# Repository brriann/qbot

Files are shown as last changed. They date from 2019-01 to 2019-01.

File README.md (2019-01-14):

# qbot
Build a Self-Driving Q-Bot using a Raspberry Pi Zero-W

Here is an overview of the project: https://medium.com/@michael_87060/build-a-self-driving-q-bot-6aa67ba60769

(and here is an older repo that supports a BeagleBone Blue: https://github.com/jvon-challenges/qbot)

The Q-bot is a small robot and associated software that uses machine learning (specifically Q learning) to learn how to complete a simple task (eg, seek the nearest object in its surroundings). The training can take place in a virtual or physical environment.

The build should cost <$50 with readily-available parts, and less if you salvage. The physical robot uses a Raspberry Pi Zero W, a Sparkfun VL53L1X laser time-of-flight sensor, and 28byj geared stepper motors for movement.  Aside from assorted nuts and bolts, a battery, and some wires, the only other required components can be 3D printed.  Links are provided below to the components you will need.  These are example products or vendors only; feel free to substitute parts wherever you like.  We are not endorsing, sponsored by,  or recommending any particular seller.

- Raspberry Pi Zero W: 
https://www.adafruit.com/product/3708

- 28byj Steppers with drivers: 
https://www.amazon.com/dp/B06X982PSL

- VL53L1x ToF distance sensor:
https://www.sparkfun.com/products/14722

- M3 hardware assortment:
https://www.amazon.com/gp/product/B07CZBR66J

- F to F dupont wires:
https://www.amazon.com/dp/B07GD2BWPY

For power, any small USB battery pack will be enought to run the bot. I used a 2S lipo 
battery and a BEC (battery eliminator) because I had them on hand for other projects, but
a small flat USB power bank is probably easier because no special charger is needed.

- USB battery pack:
https://www.amazon.com/dp/B076HJTNYJ/

- 2S lipo example:
https://www.amazon.com/dp/B07BJZZYBY

- BEC example: 
https://www.amazon.com/gp/product/B074PM59YS/

A video walkthrough of the build can be found here: https://youtu.be/-1W7-Q0RIaM

There are three example files included in this repo:

- example_virtual.py will create an instance of a virtual Q-bot and it will train to seek a randomly-generated virtual obstacle.  This example does not require a physical q-bot; you can run this on your laptop or desktop and it will render the virtual bot and its obstacle on screen using the python 'turtle'.

- example-physical.py will attempt to train the physical q-bot by looking around for an obstacle and learn to move closer to it by trial and error, improving as it goes

- example_virtual_physical will create a virtual q-bot, train it in software, and then use the learned Q-table values from the software training to have the physical Q-bot seek its nearest obstacle 

Enjoy the project files, and please reach out to us with questions, comments, and stories about your work with this project!  We can't wait to hear from you.

For hardware: jeff@loislab.org
For software: michael@loislab.org

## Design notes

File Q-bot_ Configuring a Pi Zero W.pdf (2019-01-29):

## Q-Bot: Configuring a Raspberry Pi Zero W

To run headless, optionally with Cloud9

This guide assumes you have a Raspberry Pi Zero W and want to set it up to run it headless (without a monitor and keyboard) on your wireless network. In my particular case, I’m using the Pi as the “brain” for the Q-bot robot; I want to connect to it using SSH wirelessly to control it, and I want to connect to a programming environment running on the Pi with a web browser.

Getting the Pi Zero operating on your network

1. Download the latest image of Raspbian Stretch Lite: https://www.raspberrypi.org/downloads/raspbian/
2. Using Etcher (or a similar image writing application), burn the image to your SD card
3. Mount the resulting burned SD image; you should see a boot volume with a number of files inside.
4. Create a new file called wpa_supplicant.conf in the root / directory of the boot partition (the smaller of the two partitions), with the following contents:

ctrl_interface=DIR=/var/run/wpa_supplicant GROUP=netdev
update_config=1
country=US

network={
ssid="YOURSSID"
psk="YOURPASSWORD"
scan_ssid=1
key_mgmt=WPA-PSK
}
5. Create an empty file called “ssh” in the root / directory of the boot partition of the SD card. The empty file will enable ssh, and will be deleted upon the next startup. Here are the notes from: https://www.raspberrypi.org/documentation/remote-access/ssh/

Enable SSH on a headless Raspberry Pi (add file to SD card on another machine)

For headless setup, SSH can be enabled by placing a file named ssh, without any extension, onto the boot partition of the SD card from another computer. When the Pi boots, it looks for the ssh file. If it is found, SSH is enabled and the file is deleted. The content of the file does not matter; it could contain text, or nothing at all.

If you have loaded Raspbian onto a blank SD card, you will have two partitions. The first one, which is the smaller one, is the boot partition. Place the file into this one.

6. Also in the root / directory of the boot partition, edit the config.txt file, and add the following lines at the end:
# Enable UART

enable_uart=1
7. Unmount the image and put the SD in the raspberry pi. Power it up and wait a couple of minutes.
8. If all goes well, the device will register it on your local network using mDNS and appear as “raspberrypi.local”. You can ping and ssh into the device now.
9. Alternatively: log into the Raspberry Pi using SSH:
user = pi, password = raspberry, ip address = [address on local subnet], example:
> pi@192.168.0.107
pi@192.168.0.107's password: raspberry

If the device doesn’t show up, then you need to go into troubleshooting mode. For example, if you’re working on a small local network where you don’t have a network admin to yell at you for running scans, you can power off the device and run an nmap scan (“sudo nmap -sn 192.168.0.0/24”) to identify devices on your local subnet. Boot the Pi Zero and scan again, and chances are that any new device is your Pi.

If THAT doesn’t work, try the following:
1. Try rebooting the Pi and see if that fixes it. Be patient on the first boot, it might take a few minutes.
2. Your wireless network might use a different authentication type. In the wpa_supplicant.conf file above, I was connecting to a network that used WPA Personal authentication, so I used the line “key_mgmt=WPA-PSK”. If you’re using WPA Enterprise, it needs to change to “key_mgmt=WPA-EAP”. If you’re using something else, google it.

Updating the OS and installing Cloud9
Cloud9 is a web-based development environment. It’s much more convenient when writing code for a project like the Q-bot compared to using something like a native editor like nano or vi in an SSH session. Setting it up takes some time, and consumes resources on a computer that isn’t exactly a powerhouse to begin with, so if you don’t want it or need it, feel free to skip ahead.
1. Reboot the Pi

2. Log into the Pi and run:

sudo apt-get update && sudo apt-get upgrade

Be patient, it might take a while.

3. From your home directory, grab the NodeJS ARM package and extract it to /usr/local:

cd ~

wget http://nodejs.org/dist/v0.10.28/node-v0.10.28-linux-arm-pi.tar.gz

tar -xzf ~/node-v0.10.28-linux-arm-pi.tar.gz

cd node-v0.10.28-linux-arm-pi/

sudo cp -rf * /usr/local

export NODE_PATH=”/usr/local/lib/node_modules”

4. Grab a copy of Cloud9 from Git and build it:

git clone git://github.com/c9/core.git c9sdk cd c9sdk
scripts/install-sdk.sh
5. Once that’s done, you can launch Cloud9 any time you want to use it by running the following command from the prompt:

~/c9sdk/server.js -l 0.0.0.0 -a : -w $MY_PROJECT_PATH &

Once all of those installations are complete, you should be able to use Cloud9 via web browser, and use the Adafruit library and example code to control servos and ESCs from the Pi.

Other Required Libraries

Update Python:

sudo apt-get update
sudo apt-get install -y python3 python3-pip python-dev sudo pip3 install rpi.gpio

Install support for i2c (a 2-wire serial protocol):

sudo apt-get install python-smbus sudo apt-get install i2c-tools

Python library for the vl53l1x laser distance sensor:

sudo pip3 install smbus2

sudo pip install vl53l1x

Install numpy:

sudo pip3 install numpy

Sometimes the install doesn’t work using pip3; if so, try:

sudo apt-get install python3-numpy

Enjoy the project files, and please reach out to us with questions, comments, and stories about your work with this project! We can't wait to hear from you.

For hardware: jeff@loislab.org
For software: michael@loislab.org

Reference:

This guide leans heavily on the information provided in the articles below. Thank you to the authors who shared their knowledge and made this guide (and the project overall) possible.

Adafruit’s guide Pi Zero W headless config: https://learn.adafruit.com/raspberry-pi-zero-creation/overview

Chintan Pathak’s guide to installing Cloud9 on a Raspberry Pi: https://medium.com/@chintanp/using-cloud9-3-0-ide-on-raspberry-pi-954cf2d6ab8e

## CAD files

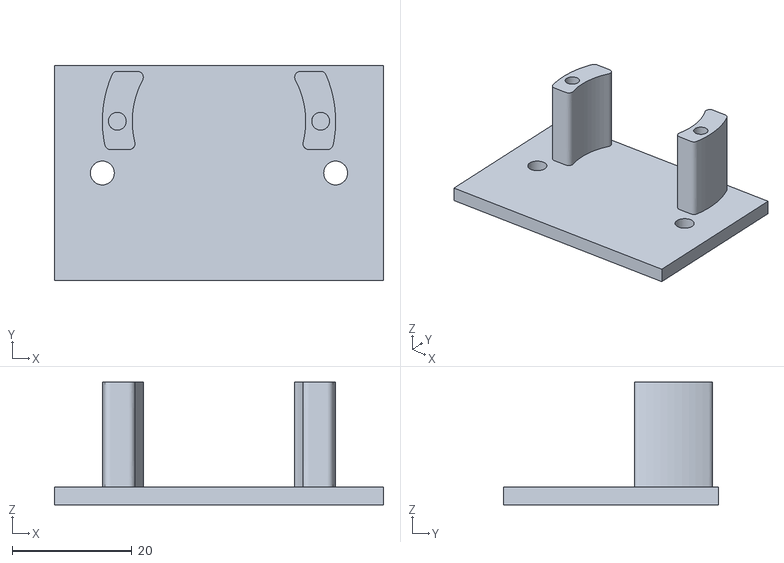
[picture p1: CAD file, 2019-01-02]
CAD/28byj sensor mount.stl
55.0 x 36.0 x 20.5

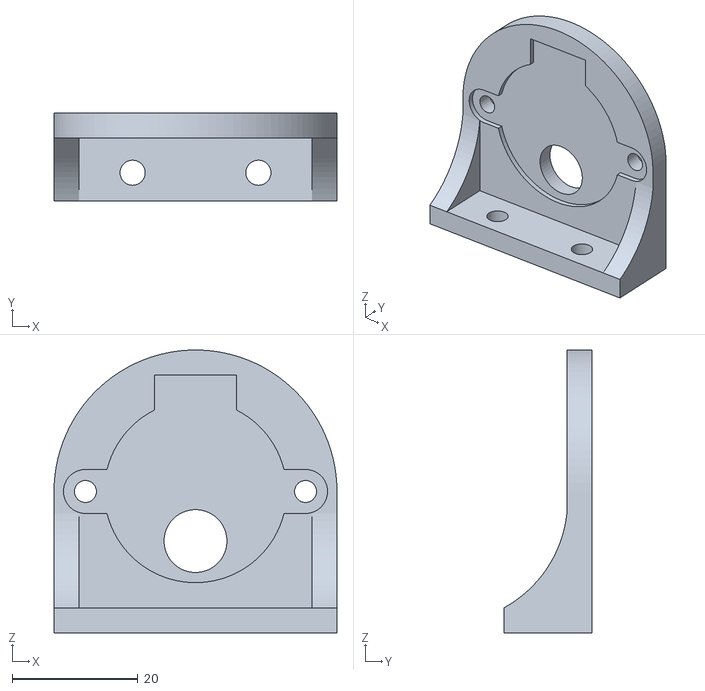
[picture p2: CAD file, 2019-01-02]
CAD/28byj bracket.stl
45.0 x 14.0 x 45.0

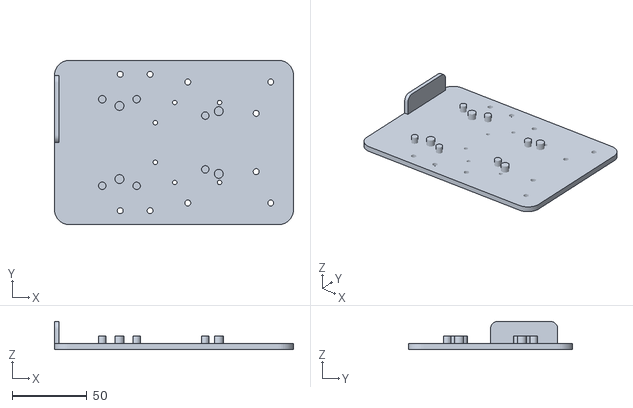
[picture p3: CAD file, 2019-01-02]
CAD/Qbot frame Rev3.stl
160.0 x 110.0 x 19.0

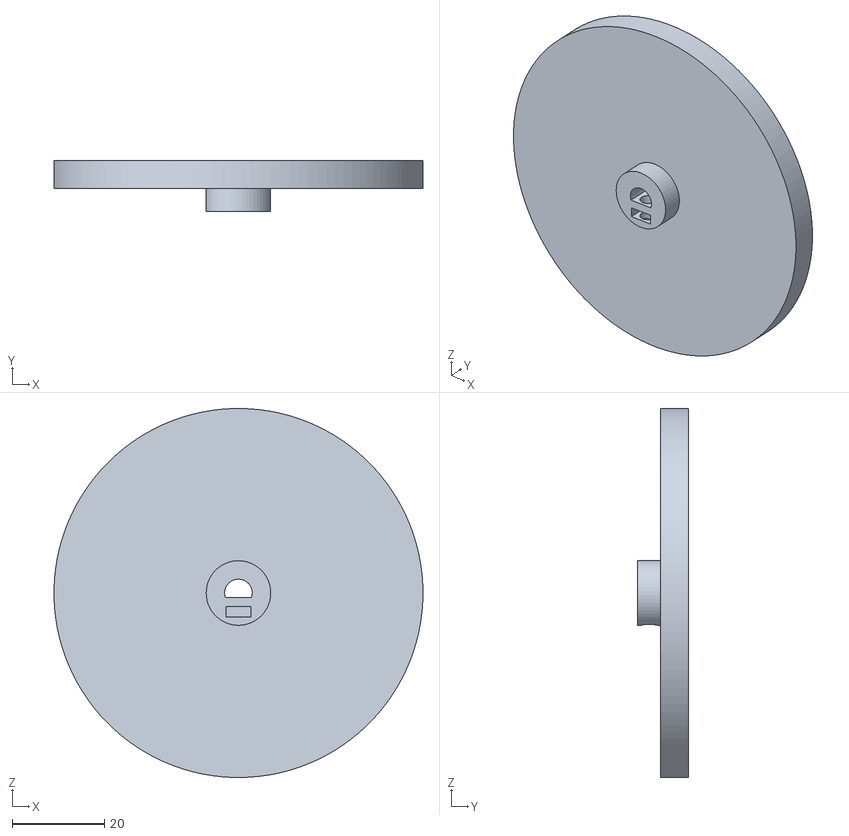
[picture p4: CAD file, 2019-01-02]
CAD/Qbot wheel Rev2.stl
80.0 x 11.0 x 80.0

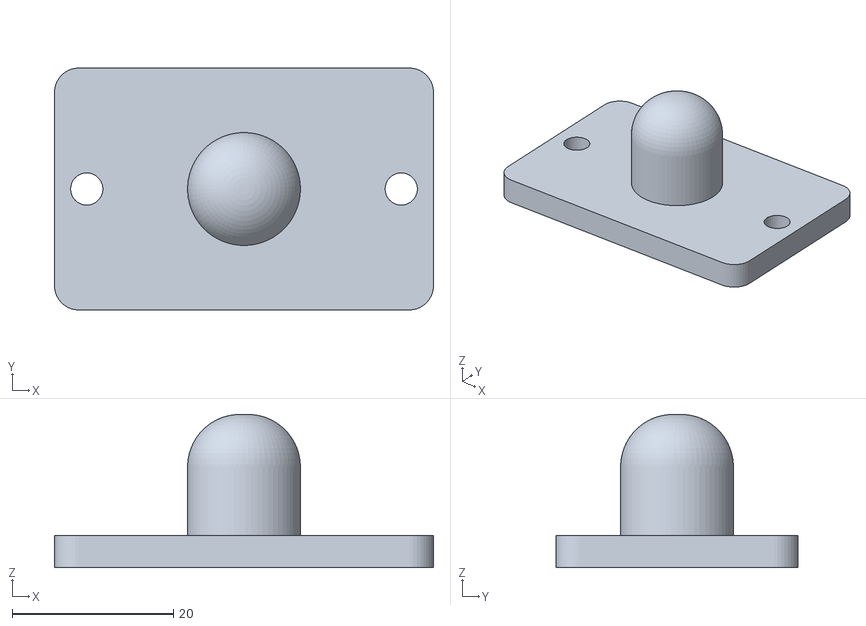
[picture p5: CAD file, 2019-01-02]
CAD/Front skid.stl
47.0 x 30.0 x 19.0

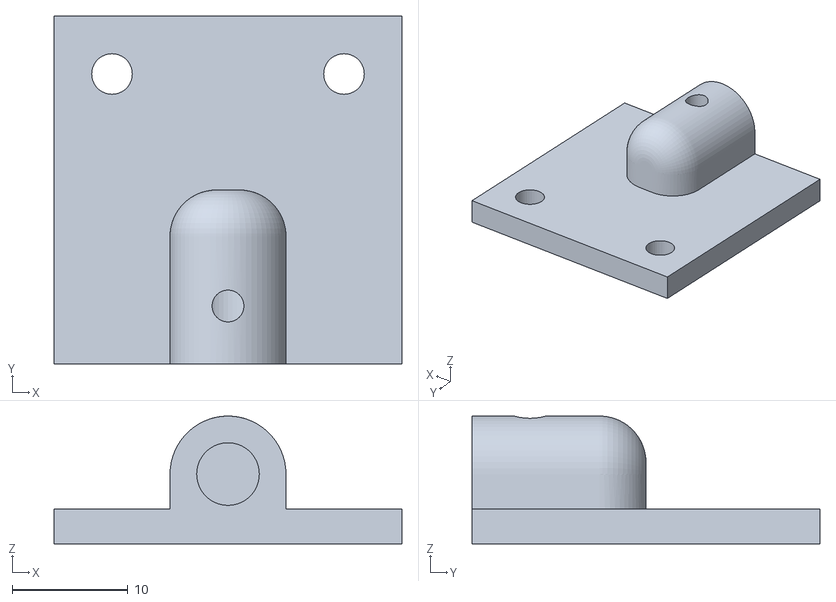
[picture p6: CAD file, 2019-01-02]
CAD/Lidar mount.stl
30.0 x 30.0 x 11.0

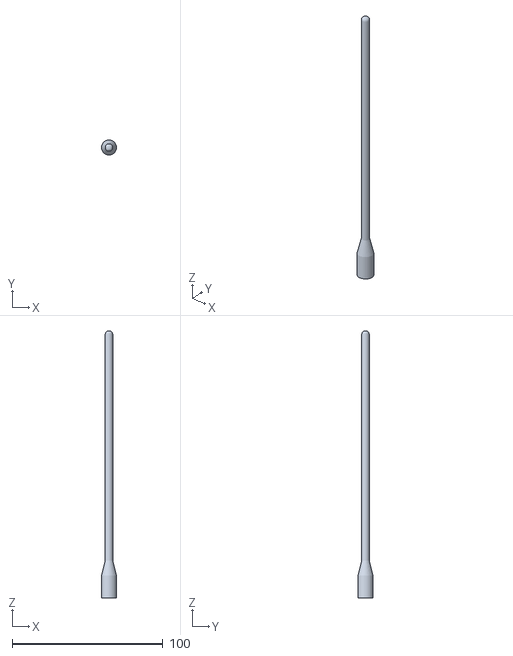
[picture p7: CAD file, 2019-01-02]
CAD/Lidar extension.stl
9.95 x 10.0 x 177.4

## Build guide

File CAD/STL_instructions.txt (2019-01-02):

The STL files in this folder can be printed to construct the frame for our 
Q-learning robot. It is intended to be built with 28byj stepper motors and
a Raspberry Pi.  Other parts, like motors, can be used but you'll have to make 
your own mounts or modify these ones. 

For a 28byj motor build, print the following:
- Qbot frame
- 28byj sensor motor mount
- Lidar extension
- Lidar mount  
- 28byj bracket for the wheel motors
- Qbot wheel for 28byj motors
- Front skid (if not using a ball caster)

For the front wheel,I used a 'ball caster', available on 
Amazon or eBay. Mine has a 40mm spacing between the mounting holes to line
up with the lidar motor mount holes.  You can use something else and drill
new holes, or print the "front skid" part for a static skid-style
third wheel.

I printed my parts with 0.2mm layer height and 30% infill on an Original 
Prusa i3 Mk3 printer. Your printer will be a little different, but about the 
only thing that would vary would be interior holes for fasteners - just drill
them out if they don't fit.

The robot was designed to be assembled with M3 hardware.  You can use 
something else, just widen the holes to fit and make sure the bolts don't 
interfere with movement if you substitute longer bolts.  

Don't be afraid to hack/modify/copy these parts to suit your build.  They're
designed to suit my particular needs and ideas, and yours might be different.
Experiment!

Email us with questions - it's why we're here:
Hardware - jeff@jvon.org
Software - michael@jvon.org

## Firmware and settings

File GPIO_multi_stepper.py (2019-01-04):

import RPi.GPIO as GPIO
from time import sleep
from collections import deque

class StepperMotors:
  
  halfStepSequence = (
    (1, 0, 0, 0),
    (1, 1, 0, 0),
    (0, 1, 0, 0),
    (0, 1, 1, 0),
    (0, 0, 1, 0),
    (0, 0, 1, 1),
    (0, 0, 0, 1),
    (1, 0, 0, 1)
  )
  
  delay = 0.0005

  def __init__(self, pin_sets):
    self.pin_sets = pin_sets
    GPIO.setmode(GPIO.BOARD)
    self.positions = [0 for x in range(len(pin_sets))]
    self.degrees_per_step = 0.0875
    self.dq = [deque(StepperMotors.halfStepSequence) for i in range(len(pin_sets))]
    for pin_group in self.pin_sets:
      for pin in pin_group:
        GPIO.setup(pin, GPIO.OUT)
        GPIO.output(pin, 0)

  def doStep(self, directions):
    for j, pin_group in enumerate(self.pin_sets):
      self.dq[j].rotate(directions[j])
      for k in range(4):
        GPIO.output(pin_group[k], self.dq[j][0][k])
        self.positions[j] += self.degrees_per_step * directions[j]
    sleep(StepperMotors.delay)

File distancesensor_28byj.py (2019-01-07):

from stepper import Stepper
import numpy as np
import VL53L1X
import math
import time

################################################################################
#                                                                              #
# Distance Sensor using SparkFun                                               #
#   see: https://www.sparkfun.com/products/14722                               #
#                                                                              #
################################################################################

class DistanceSensor:

    pins = (19,21,23,24)

    def __init__(self, motor):
        self.position = 0.0  # 0 is forward
        self.lidar = VL53L1X.VL53L1X(i2c_bus=1, i2c_address=0x29)
        self.lidar.open() # Initialise the i2c bus and configure the sensor
        self.motor = motor

    def get_reading(self, position):
        self.seek_position(position)
        return self.motor.get_position(), self.read_distance()

    def seek_position(self, target):
        self.motor.set_target(target)
        while self.motor.has_steps():
            self.motor.do_step()

    def read_distance(self):
        distance_in_mm = 0
        self.lidar.start_ranging(3) # Start ranging, 1 = Short Range, 2 = Medium Range, 3 = Long Range
        for n in range(5):
            distance_in_mm += self.lidar.get_distance()
        distance_in_mm /= 5.0
        self.lidar.stop_ranging() # Stop ranging
        return distance_in_mm

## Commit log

2019-01-02 Raspberry Pi build with 28byj steppers
    [28byj bracket.stl, 28byj sensor mount.stl, Front skid.stl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]
2019-01-02 Removed old Beagle files
    [Qbot Frame.stl, Qbot Nema11 holder for lidar.stl, Qbot bracket for 28byj stepper motor.stl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]
2019-01-07 Stepper control changes
2019-01-09 added CW/CCW stepper parameters
